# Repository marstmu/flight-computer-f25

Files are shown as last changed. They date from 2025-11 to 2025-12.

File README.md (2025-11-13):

# MARS Flight Computer F25

Use Export KiCad Images Workflow

---

<div align="center">
  <div>
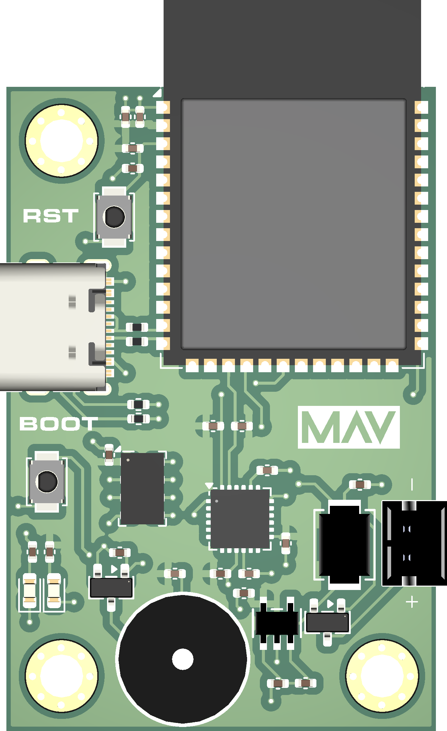
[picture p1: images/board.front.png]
    
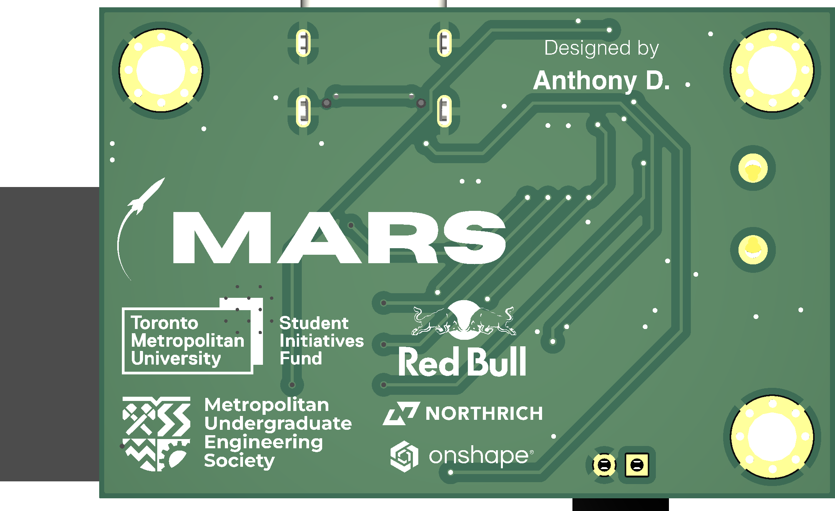
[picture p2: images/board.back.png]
    
    <p><em>3D Render</em></p>
  </div>
  <br>

  <div>
    Schematic<br>
    <p><em>Schematic</em></p>
  </div>
  <br>
  
  <div>
    Front
    Back<br>
    <em>Footprint</em>
  </div>
</div>

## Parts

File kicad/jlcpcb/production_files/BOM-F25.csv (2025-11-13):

Comment | Designator | Footprint | LCSC | Quantity
0.1uF | C2,C5,C7,C9 | C_0402_1005Metric | C1525 | 4
100k | R5,R8,R9 | C_0402_1005Metric | C25741 | 3
10k | R11 | C_0402_1005Metric | C25744 | 1
10nF | C4 | C_0402_1005Metric | C15195 | 1
10uF | C1,C10,C8 | C_0402_1005Metric | C15525 | 3
1k | R1,R4 | C_0402_1005Metric | C11702 | 2
1uF | C3 | C_0402_1005Metric | C52923 | 1
2.2nF | C6 | C_0402_1005Metric | C84703 | 1
27 | R16,R17 | R_0402_1005Metric | C25100 | 2
2k | R7 | C_0402_1005Metric | C4109 | 1
4.7k | R2,R3 | C_0402_1005Metric | C25900 | 2
5.1k | R12,R6 | R_0402_1005Metric | C25905 | 2
AP2112K-3.3 | U5 | SOT_RG1_DIO | C3021085 | 1
B2B-PH-K-S | J3 | JST_B2B-PH-K-S | C131337 | 1
BOOT | SW2 | SW_SPST_B3U-1000P | C231329 | 1
DMG3415U | Q2 | SOT-23 | C7202986 | 1
ESP32-S3-WROOM-1-N8 | U4 | ESP32-S3-WROOM-1 | C2913198 | 1
HNB09A03 | LS1 | HNB09A03 | C96102 | 1
IRLML6244 | Q1 | SOT-23 | C5123965 | 1
LED | D1 | LED_0603_1608Metric | C2288 | 1
LED | D2 | LED_0603_1608Metric | C2290 | 1
MBRS130LT3G | CR1 | DIODE_SMB_2L_ONS | C51771 | 1
MPU-6050 | U2 | InvenSense_QFN-24_4x4mm_P0.5mm | C24112 | 1
MS5611-01BA | U1 | LGA-8_3x5mm_P1.25mm | C15639 | 1
RESET | SW1 | SW_SPST_B3U-1000P | C231329 | 1
USB_C_Receptacle_USB2.0_16P | J4 | USB_C_Receptacle_Palconn_UTC16-G | C2765186 | 1

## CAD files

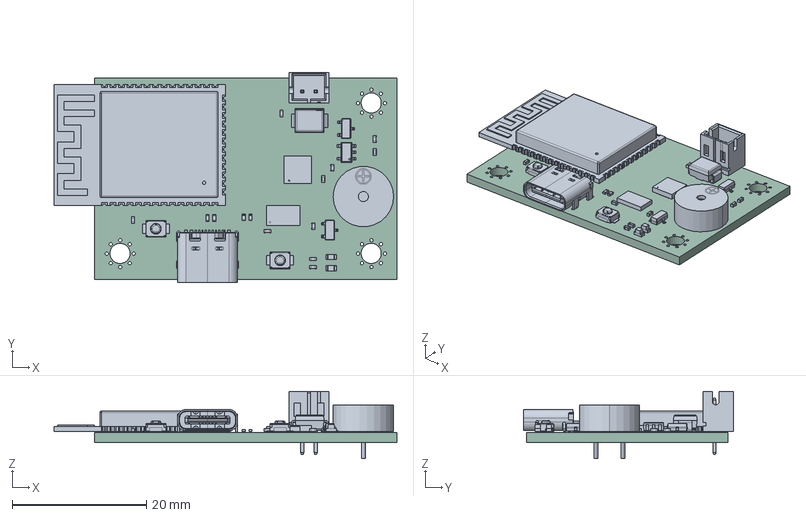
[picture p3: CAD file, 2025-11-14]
images/board.step
51.1 x 31.2 x 10.0 mm
C_0402_1005Metric x 10
SOT-23 x 2
kicad_embedded_C2CC4DB59B260F51541E3CE257640357
ESP32-S3-WROOM-1
board 1.6
R_0402_1005Metric x 4
USB_C_Receptacle_GCT_USB4105-xx-A_16P_TopMnt_Horizontal
LED_0603_1608Metric x 2
MBRS130LT3G
LGA-8_3x5mm_P1.25mm
SW_SPST_B3U-1000P x 2
AP2112K-3.3TRG1--3DModel-STEP-418109
F25_PCB

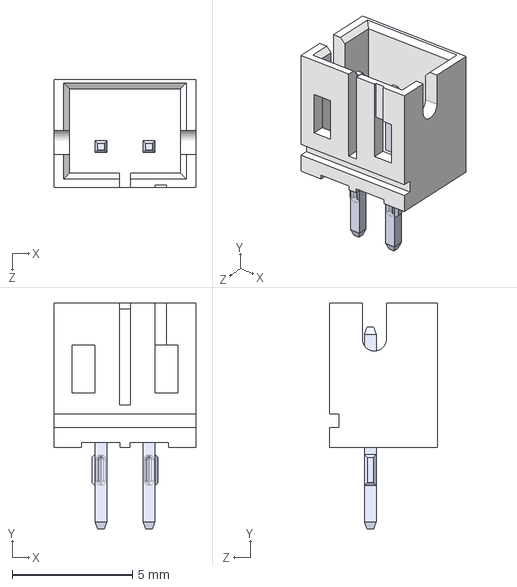
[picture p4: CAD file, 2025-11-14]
kicad/step files/B2B-PH-K-S--3DModel-STEP-56544.STEP
5.90 x 9.40 x 4.50 mm

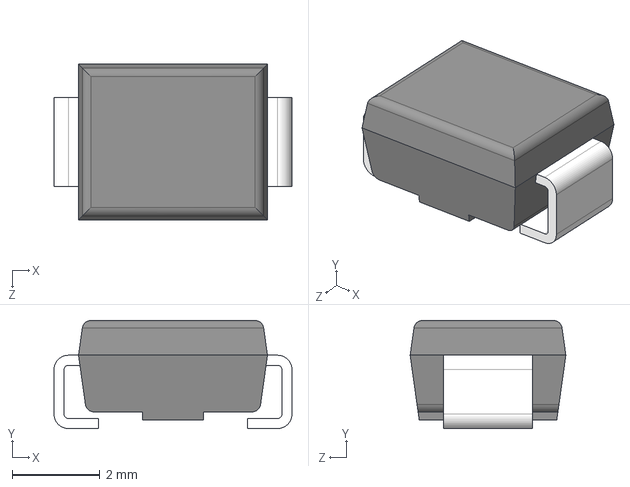
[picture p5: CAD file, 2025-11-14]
kicad/step files/MBRS130LT3G.STEP
5.44 x 2.47 x 3.56 mm

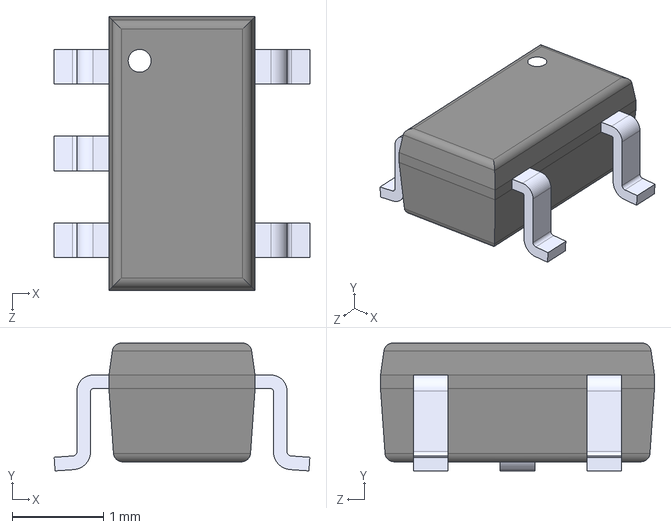
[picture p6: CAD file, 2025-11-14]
kicad/step files/AP2112K-3.3TRG1--3DModel-STEP-418109.STEP
2.80 x 1.40 x 3.00 mm

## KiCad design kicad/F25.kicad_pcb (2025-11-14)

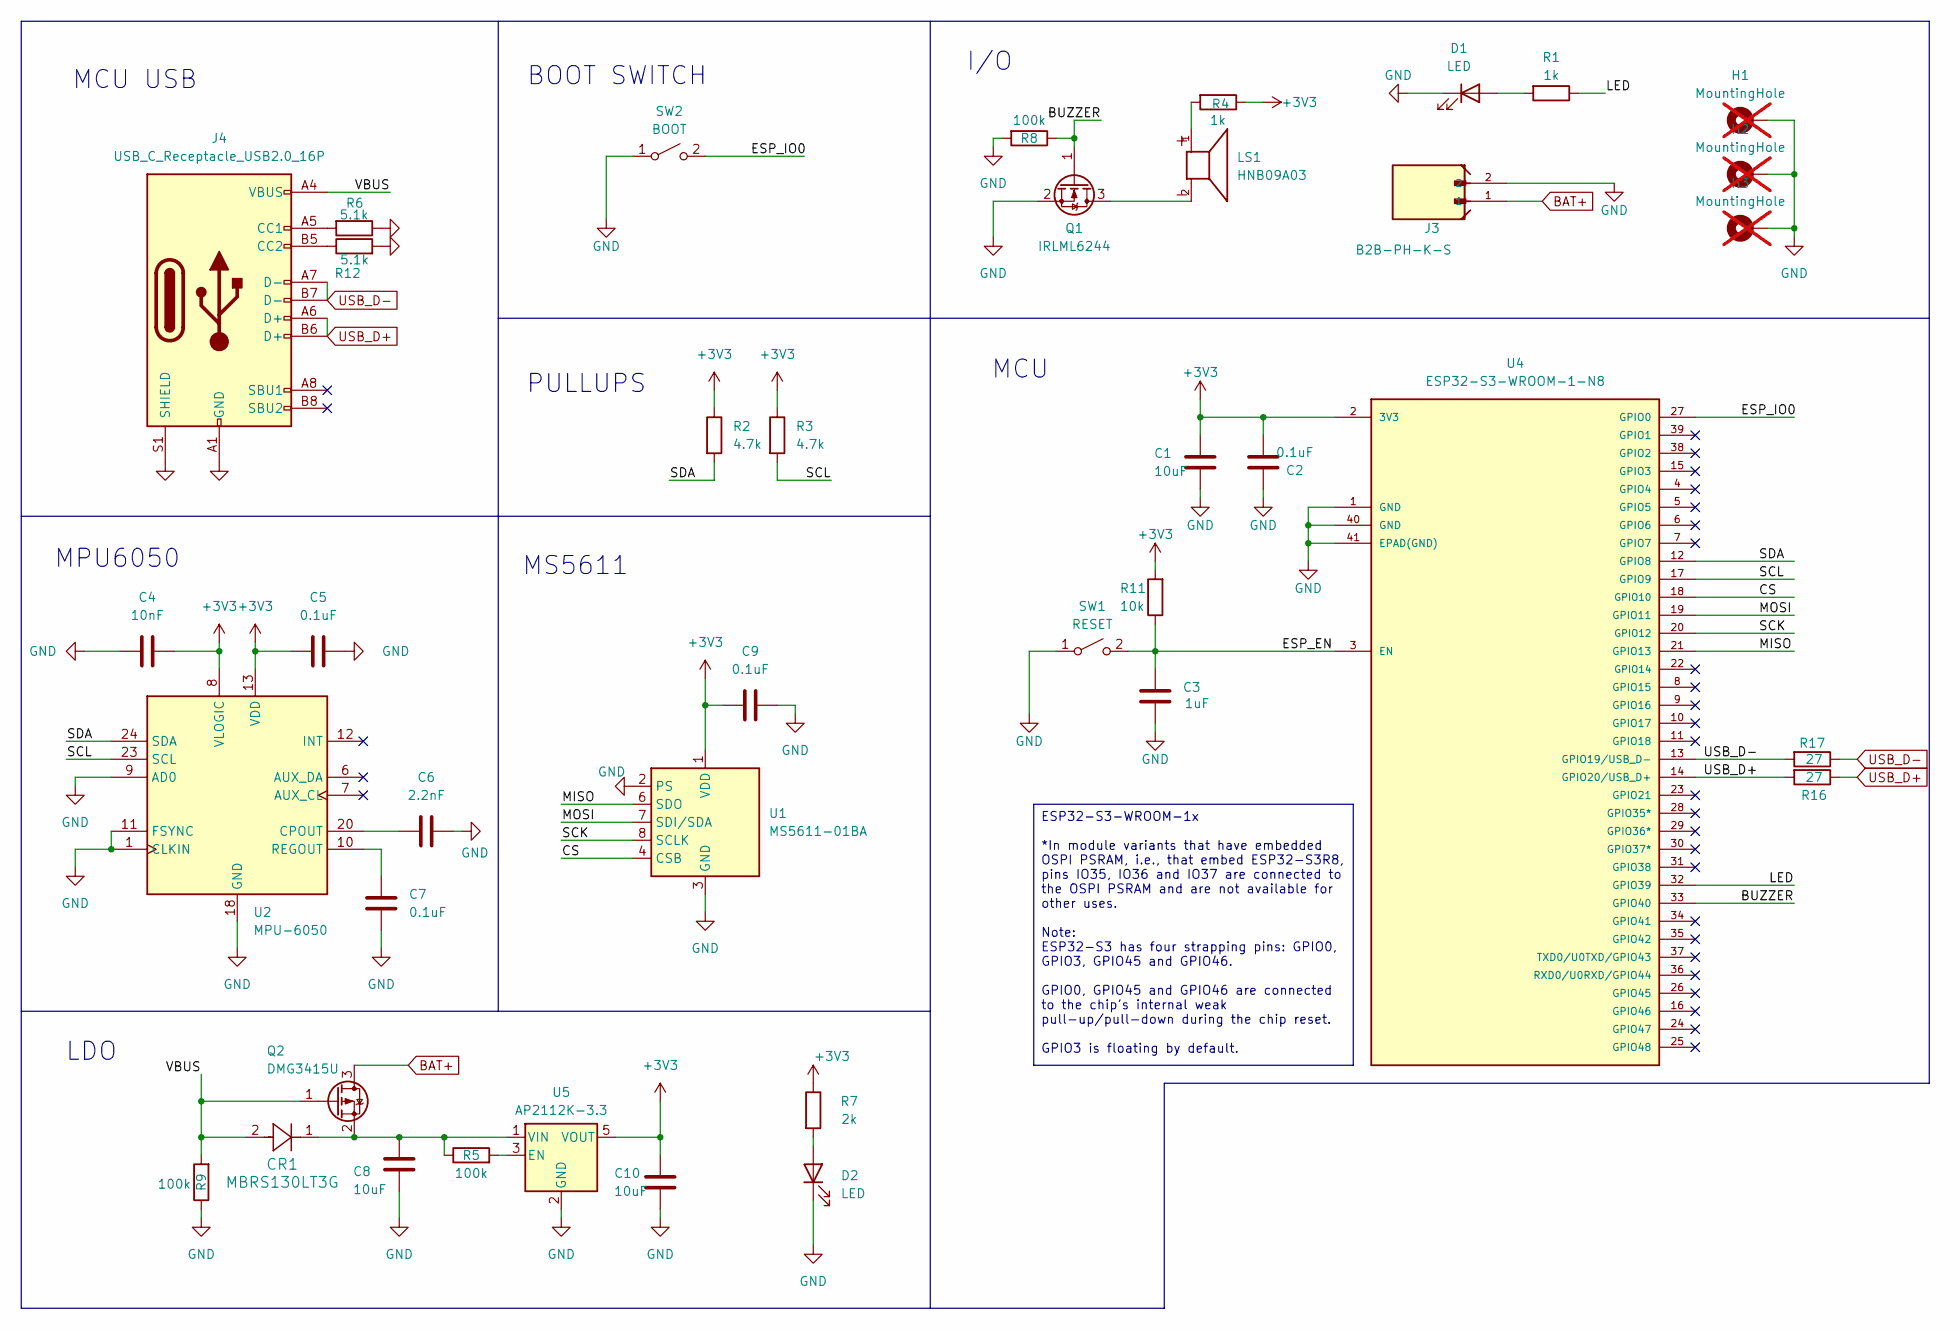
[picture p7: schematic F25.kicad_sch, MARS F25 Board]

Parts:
C1, C8, C10: 10uF; C_0402_1005Metric; LCSC C15525
C2, C5, C7, C9: 0.1uF; C_0402_1005Metric; LCSC C1525
C3: 1uF; C_0402_1005Metric; LCSC C52923
C4: 10nF; C_0402_1005Metric; LCSC C15195
C6: 2.2nF; C_0402_1005Metric; LCSC C84703
CR1: MBRS130LT3G; DIODE_SMB_2L_ONS; LCSC C51771
D1: LED; LED_0603_1608Metric; LCSC C2288
D2: LED; LED_0603_1608Metric; LCSC C2290
H1, H2, H3: MountingHole; hole; not fitted
J3: B2B-PH-K-S; JST_B2B-PH-K-S; LCSC C131337
J4: USB_C_Receptacle_USB2.0_16P; USB_C_Receptacle_Palconn_UTC16-G; LCSC Part # C2765186
LS1: HNB09A03; PARTREV C; LCSC C96102
Q1: IRLML6244; SOT-23; LCSC C5123965
Q2: DMG3415U; SOT-23; LCSC C7202986
R1, R4: 1k; C_0402_1005Metric; LCSC C11702
R2, R3: 4.7k; C_0402_1005Metric; LCSC C25900
R5, R8, R9: 100k; C_0402_1005Metric; LCSC C25741
R6, R12: 5.1k; R_0402_1005Metric; LCSC Part # C25905
R7: 2k; C_0402_1005Metric; LCSC C4109
R11: 10k; C_0402_1005Metric; LCSC C25744
R16, R17: 27; R_0402_1005Metric; LCSC Part # C25100
SW1: RESET; SW_SPST_B3U-1000P; LCSC C231329
SW2: BOOT; SW_SPST_B3U-1000P; LCSC C231329
U1: MS5611-01BA; LGA-8_3x5mm_P1.25mm; LCSC C15639
U2: MPU-6050; InvenSense_QFN-24_4x4mm_P0.5mm; LCSC C24112
U4: ESP32-S3-WROOM-1-N8; ESP32-S3-WROOM-1; LCSC C2913198
U5: AP2112K-3.3; SOT_RG1_DIO; LCSC C3021085

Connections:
+3V3: C1.2, C2.2, C4.2, C5.2, C9.1, C10.2, R2.1, R3.1, R4.1, R7.1, R11.2, U1.1 (VDD), U2.8 (VLOGIC), U2.13 (VDD), U4.2 (3V3), U5.5 (VOUT)
/BUZZER: Q1.1 (G), R8.1, U4.33 (GPIO40)
/CS: U1.4 (CSB), U1.5 (CSB), U4.18 (GPIO10)
/ESP_EN: C3.1, R11.1, SW1.2 (B), U4.3 (EN)
/ESP_IO0: SW2.2 (B), U4.27 (GPIO0)
/LED: R1.1, U4.32 (GPIO39)
/MISO: U1.6 (SDO), U4.21 (GPIO13)
/MOSI: U1.7 (SDI/SDA), U4.19 (GPIO11)
/SCK: U1.8 (SCLK), U4.20 (GPIO12)
/SCL: R3.2, U2.23 (SCL), U4.17 (GPIO9)
/SDA: R2.2, U2.24 (SDA), U4.12 (GPIO8)
/VBUS: CR1.2, J4.A4 (VBUS), J4.A9 (VBUS), J4.B4 (VBUS), J4.B9 (VBUS), Q2.1 (G), R9.2
BAT+: J3.1, Q2.3 (D)
GND: C1.1, C2.1, C3.2, C4.1, C5.1, C6.2, C7.2, C8.1, C9.2, C10.1, D1.1 (K), D2.1 (K), H1.1, H2.1, H3.1, J3.2, J4.A1 (GND), J4.A12 (GND), J4.B1 (GND), J4.B12 (GND), J4.S1 (SHIELD), Q1.2 (S), R6.1, R8.2, R9.1, R12.2, SW1.1 (A), SW2.1 (A), U1.2 (PS), U1.3 (GND), U2.1 (CLKIN), U2.9 (AD0), U2.11 (FSYNC), U2.18 (GND), U4.1 (GND), U4.40 (GND), U4.41 (EPAD(GND)), U5.2 (GND)
unnamed: D1.2 (A), R1.2
unnamed: D2.2 (A), R7.2
unnamed: J4.A5 (CC1), R6.2
unnamed: J4.B5 (CC2), R12.1
unnamed: LS1.1, R4.2
unnamed: LS1.2, Q1.3 (D)
unnamed: C8.2, CR1.1, Q2.2 (S), R5.1, U5.1 (VIN)
unnamed: C6.1, U2.20 (CPOUT)
unnamed: C7.1, U2.10 (REGOUT)
unnamed: R5.2, U5.3 (EN)
USB_D+: J4.A6 (D+), J4.B6 (D+), R16.1, R16.2, U4.14 (GPIO20/USB_D+)
USB_D-: J4.A7 (D-), J4.B7 (D-), R17.1, R17.2, U4.13 (GPIO19/USB_D-)

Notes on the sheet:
I/O
MCU
PULLUPS
MPU6050
BOOT SWITCH
MS5611
LDO
MCU USB
ESP32-S3-WROOM-1x *In module variants that have embedded OSPI PSRAM, i.e., that embed ESP32-S3R8, pins IO35, IO36 and IO37 are connected to the OSPI PSRAM and are not available for other uses. Note: ESP32-S3 has four strapping pins: GPIO0, GPIO3, GPIO45 and GPIO46. GPIO0, GPIO45 and GPIO46 are conn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

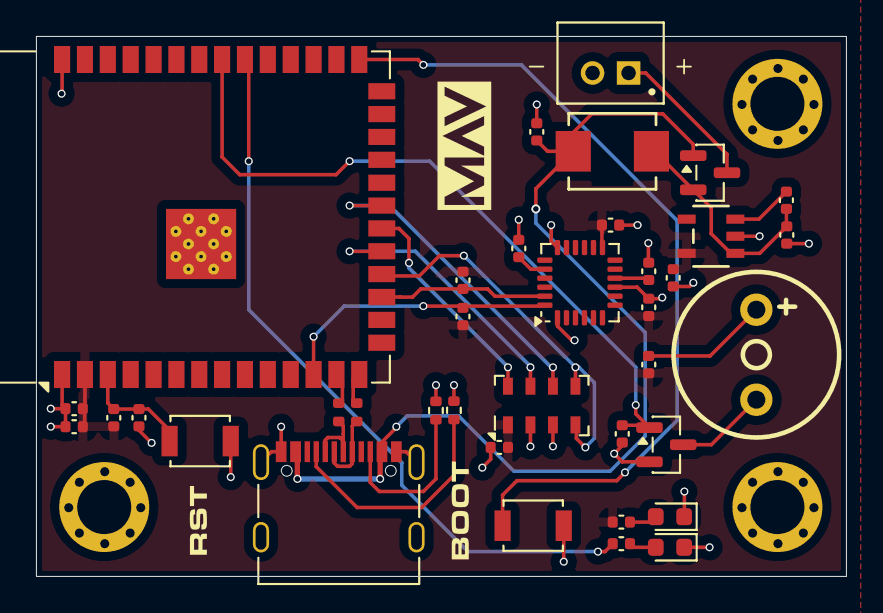
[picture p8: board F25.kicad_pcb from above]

Board: 2 copper layers, 45.0 x 30.0 mm, 40 parts (0 on the bottom side), 26 nets.

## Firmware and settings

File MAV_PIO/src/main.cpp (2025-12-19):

/*
   MARS BOARD MAV - ESP32-S3 Flight Computer (PlatformIO)

   SAFE MODE (No USB MSC):
   - Pre-launch RAM cache (ring buffer) so you get data before launch
   - Launch detection -> open a new CSV and dump cache
   - Apogee detection -> mark event in CSV
   - Landing detection -> log a bit more -> close file
   - After file is closed -> start WiFi AP + Web dashboard + download endpoints

   MS5611:
   - Non-blocking sampling state machine (no delays in handlers)
   - Second-order temperature compensation
   - ASL altitude: altitude_asl = ref_alt_asl + delta_h
*/

#include <Arduino.h>
#include <Wire.h>
#include <ms5611.h>
#include <WiFi.h>
#include <WebServer.h>
#include <FFat.h>
#include <esp_system.h> // esp_random()

#include <I2Cdev.h>
#include <MPU6050_6Axis_MotionApps20.h>
#include <helper_3dmath.h>

// -------------------- PIN CONFIG --------------------
const int SDA_PIN = 8;
const int SCL_PIN = 9;



const int LED_PIN = 39;

// -------------------- ACCESS POINT --------------------
const char* ap_ssid = "MAV_TELEM";
const char* ap_pass = "RocketGroup1!"; // must be >=8 chars
WebServer server(80);
bool apMode = false;

// If true: AP runs pre-launch for setup; turns off during flight; turns back on after landing.
static constexpr bool WIFI_ON_GROUND = true;
static constexpr bool WIFI_OFF_DURING_FLIGHT = false;

// -------------------- MPU6050 DMP --------------------
MPU6050 mpu;
bool dmpReady = false;
uint8_t fifoBuffer[64];
uint16_t packetSize = 0;

Quaternion q;
VectorFloat gravity;
float ypr[3];   // yaw, pitch, roll (rad)
float ypr_offset[3] = {0, 0, 0};

int16_t ax_raw, ay_raw, az_raw;
int16_t gx_raw, gy_raw, gz_raw;
int16_t temp_raw;
float temp_mpu;

// MPU6050 scaling
const float ACCEL_SCALE = 2048.0f; // ±16g
const float GYRO_SCALE  = 16.4f;   // ±2000deg/s

// Device offsets
const int16_t DEV_ACCEL_X_OFFSET = 844;
const int16_t DEV_ACCEL_Y_OFFSET = 1341;
const int16_t DEV_ACCEL_Z_OFFSET = 743;
const int16_t DEV_GYRO_X_OFFSET  = 30;
const int16_t DEV_GYRO_Y_OFFSET  = 67;
const int16_t DEV_GYRO_Z_OFFSET  = -3;

// -------------------- LED CONTROL --------------------
unsigned long lastBlinkTime = 0;
const unsigned long BLINK_FAST = 150;
const unsigned long BLINK_SLOW = 1000;

// -------------------- FLIGHT STATE / LOGGING --------------------
enum FlightState : uint8_t {
  ST_GROUND = 0,  // cache; (optional) AP on for setup
  ST_FLIGHT = 1,  // logging; AP off
  ST_LANDED = 2,  // post-land logging window
  ST_DONE   = 3   // file closed; AP on for download
};

FlightState flightState = ST_GROUND;

// Logging cadence
static constexpr uint32_t LOG_HZ = 50;
static constexpr uint32_t LOG_INTERVAL_MS = 1000 / LOG_HZ;

// Pre-launch cache
static constexpr uint32_t CACHE_SECONDS = 4;
static constexpr uint16_t CACHE_SAMPLES = LOG_HZ * CACHE_SECONDS;

// Detection tuning (adjust after ground tests)
static constexpr float LAUNCH_ALT_THRESH_M = 8.0f;
static constexpr float LAUNCH_VEL_THRESH_MPS = 8.0f;
static constexpr uint16_t LAUNCH_CONFIRM_SAMPLES = 5;

static constexpr float APOGEE_VEL_NEG_THRESH_MPS = -1.5f;
static constexpr float APOGEE_DROP_THRESH_M = 1.5f;
static constexpr uint16_t APOGEE_CONFIRM_SAMPLES = 8;

static constexpr float LAND_VEL_ABS_THRESH_MPS = 2.0f;
static constexpr float LAND_ALT_RANGE_M = 2.0f;
static constexpr uint32_t LAND_STABLE_MS = 2500;
static constexpr uint32_t LAND_AFTER_APOGEE_DELAY_MS = 8000; // 5–10s (pick 5000..10000)

static constexpr uint32_t POST_LAND_LOG_MS = 3000;

struct Sample {
  uint32_t t_ms;
  float h_m;        // height (relative to start), m
  float alt_asl_m;  // ASL altitude, m
  float vel_mps;    // filtered vertical speed, m/s
  float p_mbar;
  float t_ms5611_c;
  float t_mpu_c;
  float ax_g, ay_g, az_g;
  float pitch_deg, roll_deg, yaw_deg;
};

Sample cacheBuf[CACHE_SAMPLES];
uint16_t cacheHead = 0;
bool cacheFilled = false;

File logFile;
bool logOpen = false;
char currentLogPath[40] = {0};

uint32_t nextLogMs = 0;

// Detection internals
bool launchDetected = false;
bool apogeeDetected = false;
bool landingDetected = false;

float maxHeight_m = -1e9f;
uint16_t launchConfirm = 0;
uint16_t apogeeConfirm = 0;
uint32_t apogeeAtMs = 0;

uint32_t landStableStartMs = 0;
float landAltRef = 0.0f;
uint32_t landedAtMs = 0;

// Velocity estimation (windowed average altitude -> velocity)
// Computes v = (avg(h) - avg(prev h)) / dt across a window to suppress baro noise.
static constexpr uint8_t VELWIN = 50;   // window length in samples (LOG_HZ=50 => 25 samples = 0.50 s)

float hWin[VELWIN] = {0};
uint32_t tWin[VELWIN] = {0};
uint8_t velIdx = 0;
uint8_t velCount = 0;

float lastAvgH = 0.0f;
uint32_t lastAvgT = 0;
float velfilt = 0.0f; // optional extra low-pass after windowing
// Latest computed vertical speed for dashboard (updated in loop logging cadence)
volatile float latest_vel_mps = 0.0f;

// -------------------- FORWARD DECLARATIONS --------------------


void read_mpu_raw();
void convert_accel_to_g(float &ax_g, float &ay_g, float &az_g);
void convert_gyro_to_degs(float &gx_degs, float &gy_degs, float &gz_degs);
void read_dmp();
void zeroYPR();
void get_adjusted_ypr(float &yaw_adj, float &pitch_adj, float &roll_adj);

void updateLED();
String htmlPage();
void handleRoot();
void handleSetAltitude();
void handleZeroYPR();
void handleData();
void handleDeleteLogs();

void startAPAndServer();
void handleReset();
void stopAPAndServer();

void cachePush(const Sample &s);
void dumpCacheToFile();
bool openNewLogFile();
void closeLogFileSafe();
void writeCsvHeader();
void writeCsvRow(const Sample &s, const char* eventTag);

float computeVerticalSpeed(float h_now, uint32_t now_ms);
Sample makeSample(float vel_mps_now);
const char* flightStateName(FlightState st);

void updateFlightStateAndLogging(const Sample &s);

// -------------------- MS5611 low-level --------------------


// -------------------- MPU Raw + DMP --------------------
void read_mpu_raw() {
  mpu.getMotion6(&ax_raw, &ay_raw, &az_raw, &gx_raw, &gy_raw, &gz_raw);
  temp_raw = mpu.getTemperature();
  temp_mpu = temp_raw / 340.0f + 36.53f;
}

void convert_accel_to_g(float &ax_g, float &ay_g, float &az_g) {
  ax_g = (float)ax_raw / ACCEL_SCALE;
  ay_g = (float)ay_raw / ACCEL_SCALE;
  az_g = (float)az_raw / ACCEL_SCALE;
}

void convert_gyro_to_degs(float &gx_degs, float &gy_degs, float &gz_degs) {
  gx_degs = (float)gx_raw / GYRO_SCALE;
  gy_degs = (float)gy_raw / GYRO_SCALE;
  gz_degs = (float)gz_raw / GYRO_SCALE;
}

void read_dmp() {
  if (!dmpReady) return;

  uint8_t intStatus = mpu.getIntStatus();
  uint16_t fifoCount = mpu.getFIFOCount();

  if (intStatus & 0x10) {
    mpu.resetFIFO();
    delay(10);
    return;
  }

  while (fifoCount >= packetSize) {
    mpu.getFIFOBytes(fifoBuffer, packetSize);
    mpu.dmpGetQuaternion(&q, fifoBuffer);
    mpu.dmpGetGravity(&gravity, &q);
    mpu.dmpGetYawPitchRoll(ypr, &q, &gravity);

    read_mpu_raw();
    fifoCount = mpu.getFIFOCount();
  }
}

void zeroYPR() {
  ypr_offset[0] = ypr[0] * 180.0f / M_PI;
  ypr_offset[1] = ypr[1] * 180.0f / M_PI;
  ypr_offset[2] = ypr[2] * 180.0f / M_PI;
}

void get_adjusted_ypr(float &yaw_adj, float &pitch_adj, float &roll_adj) {
  yaw_adj   = (ypr[0] * 180.0f / M_PI) - ypr_offset[0];
  pitch_adj = (ypr[1] * 180.0f / M_PI) - ypr_offset[1];
  roll_adj  = (ypr[2] * 180.0f / M_PI) - ypr_offset[2];
}

// -------------------- Logging / state --------------------
const char* flightStateName(FlightState st) {
  switch (st) {
    case ST_GROUND: return "GROUND";
    case ST_FLIGHT: return "FLIGHT";
    case ST_LANDED: return "LANDED";
    case ST_DONE:   return "DONE";
    default:        return "UNKNOWN";
  }
}

void cachePush(const Sample &s) {
  cacheBuf[cacheHead] = s;
  cacheHead = (cacheHead + 1) % CACHE_SAMPLES;
  if (cacheHead == 0) cacheFilled = true;
}

void writeCsvHeader() {
  if (!logFile) return;
  logFile.println("t_ms,h_m,alt_asl_m,vel_mps,p_mbar,t_ms5611_c,t_mpu_c,ax_g,ay_g,az_g,pitch_deg,roll_deg,yaw_deg,event");
}

void writeCsvRow(const Sample &s, const char* eventTag) {
  if (!logFile) return;

  char line[240];
  int n = snprintf(line, sizeof(line),
    "%lu,%.3f,%.3f,%.3f,%.2f,%.2f,%.2f,%.3f,%.3f,%.3f,%.2f,%.2f,%.2f,%s",
    (unsigned long)s.t_ms,
    s.h_m, s.alt_asl_m, s.vel_mps,
    s.p_mbar,
    s.t_ms5611_c, s.t_mpu_c,
    s.ax_g, s.ay_g, s.az_g,
    s.pitch_deg, s.roll_deg, s.yaw_deg,
    (eventTag ? eventTag : "")
  );
  if (n > 0) logFile.println(line);
}

void dumpCacheToFile() {
  if (!logFile) return;

  uint16_t count = cacheFilled ? CACHE_SAMPLES : cacheHead;
  uint16_t start = cacheFilled ? cacheHead : 0;

  for (uint16_t i = 0; i < count; i++) {
    uint16_t idx = (start + i) % CACHE_SAMPLES;
    writeCsvRow(cacheBuf[idx], "CACHE");
  }
}

bool openNewLogFile() {
  if (logOpen) return true;

  currentLogPath[0] = 0;

  uint32_t r = esp_random();
  uint32_t m = millis();
  snprintf(currentLogPath, sizeof(currentLogPath), "/flight_%08lX_%08lX.csv",
           (unsigned long)r, (unsigned long)m);

  logFile = FFat.open(currentLogPath, FILE_WRITE);
  if (!logFile) {
    currentLogPath[0] = 0;
    logOpen = false;
    return false;
  }

  logOpen = true;
  writeCsvHeader();
  dumpCacheToFile();
  logFile.flush();
  return true;
}

void closeLogFileSafe() {
  if (!logOpen) return;
  logFile.flush();
  logFile.close();
  logOpen = false;
}

float computeVerticalSpeed(float hnow, uint32_t nowms) {
  // Push into ring buffer
  hWin[velIdx] = hnow;
  tWin[velIdx] = nowms;
  velIdx = (uint8_t)((velIdx + 1) % VELWIN);
  if (velCount < VELWIN) velCount++;

  // Until window is full, don't output noisy velocity
  if (velCount < VELWIN) {
    lastAvgH = hnow;
    lastAvgT = nowms;
    velfilt = 0.0f;
    return 0.0f;
  }

  // Compute average altitude and average time over the window
  float sumH = 0.0f;
  uint32_t sumT = 0;
  for (uint8_t i = 0; i < VELWIN; i++) {
    sumH += hWin[i];
    sumT += tWin[i];
  }
  const float avgH = sumH / (float)VELWIN;
  const uint32_t avgT = sumT / (uint32_t)VELWIN;

  // Differentiate the averaged signal
  if (lastAvgT == 0) {
    lastAvgT = avgT;
    lastAvgH = avgH;
    return 0.0f;
  }

  uint32_t dtms = avgT - lastAvgT;
  if (dtms < 5) return velfilt; // avoid divide by tiny dt / repeated timestamps

  const float dt = dtms / 1000.0f;
  const float v = (avgH - lastAvgH) / dt;

  // Optional extra smoothing on top of the window (can set VELALPHA=1.0f to disable)
  const float VELALPHA = 0.35f;
  velfilt = VELALPHA * v + (1.0f - VELALPHA) * velfilt;

  lastAvgT = avgT;
  lastAvgH = avgH;
  return velfilt;
}

Sample makeSample(float vel_mps_now) {
  Sample s{};
  s.t_ms = millis();

  s.h_m = isfinite(height_agl_m) ? (float)height_agl_m : 0.0f;
  s.alt_asl_m = isfinite(altitude_asl_m) ? (float)altitude_asl_m : 0.0f;
  s.vel_mps = vel_mps_now;

  s.p_mbar = isfinite(ms5611_pressure_mbar) ? (float)ms5611_pressure_mbar : 0.0f;
  s.t_ms5611_c = isfinite(ms5611_temp_c) ? (float)ms5611_temp_c : 0.0f;
  s.t_mpu_c = (float)temp_mpu;

  float ax_g, ay_g, az_g;
  convert_accel_to_g(ax_g, ay_g, az_g);
  s.ax_g = ax_g; s.ay_g = ay_g; s.az_g = az_g;

  s.pitch_deg = ypr[1] * 180.0f / M_PI;
  s.roll_deg  = ypr[2] * 180.0f / M_PI;
  s.yaw_deg = ypr[0] * 180.0f / M_PI;

  return s;
}

void updateFlightStateAndLogging(const Sample &s) {
  // Always keep a cache until launch
  if (!launchDetected) cachePush(s);

  // Track max height
  if (s.h_m > maxHeight_m) maxHeight_m = s.h_m;

  // ---------------- LAUNCH DETECT ----------------
  if (!launchDetected) {
    bool cond = (s.h_m > LAUNCH_ALT_THRESH_M) && (s.vel_mps > LAUNCH_VEL_THRESH_MPS);
    if (cond) launchConfirm++;
    else if (launchConfirm > 0) launchConfirm--;

    if (launchConfirm >= LAUNCH_CONFIRM_SAMPLES) {
      launchDetected = true;
      flightState = ST_FLIGHT;

      if (openNewLogFile()) {
        writeCsvRow(s, "EVENT_LAUNCH");
        logFile.flush();
      }

      if (WIFI_OFF_DURING_FLIGHT && apMode) {
        stopAPAndServer();
      }
    }
  }

  // ---------------- FLIGHT LOGGING ----------------
  if (flightState == ST_FLIGHT && logOpen) {
    const char* tag = "";

    // APOGEE DETECT (requires descent + drop from max)
    if (!apogeeDetected) {
      bool apCond = (s.vel_mps < APOGEE_VEL_NEG_THRESH_MPS) && ((maxHeight_m - s.h_m) > APOGEE_DROP_THRESH_M);
      if (apCond) apogeeConfirm++;
      else if (apogeeConfirm > 0) apogeeConfirm--;

      if (apogeeConfirm >= APOGEE_CONFIRM_SAMPLES) {
        apogeeDetected = true;
        apogeeAtMs = millis();
        tag = "EVENT_APOGEE";
      }
    }

    writeCsvRow(s, tag);

    // Periodic flush (limits loss, avoids flush every line)
    static uint32_t lastFlushMs = 0;
    uint32_t now = millis();
    if (now - lastFlushMs >= 1000) {
      lastFlushMs = now;
      logFile.flush();
    }
  }

  // ---------------- LANDING DETECT ----------------
  if (flightState == ST_FLIGHT && apogeeDetected && !landingDetected &&
    (millis() - apogeeAtMs) >= LAND_AFTER_APOGEE_DELAY_MS) {
    bool velOk = fabsf(s.vel_mps) < LAND_VEL_ABS_THRESH_MPS;

    if (velOk) {
      if (landStableStartMs == 0) {
        landStableStartMs = s.t_ms;
        landAltRef = s.h_m;
      } else {
        bool altOk = fabsf(s.h_m - landAltRef) < LAND_ALT_RANGE_M;
        if (!altOk) {
          landStableStartMs = s.t_ms;
          landAltRef = s.h_m;
        } else if ((s.t_ms - landStableStartMs) >= LAND_STABLE_MS) {
          landingDetected = true;
          flightState = ST_LANDED;
          landedAtMs = millis();

          if (logOpen) {
            writeCsvRow(s, "EVENT_LAND");
            logFile.flush();
          }
        }
      }
    } else {
      landStableStartMs = 0;
    }
  }

  // ---------------- POST-LANDING WINDOW ----------------
  if (flightState == ST_LANDED) {
    if (logOpen) {
      writeCsvRow(s, "POST_LAND");
    }

    if (millis() - landedAtMs >= POST_LAND_LOG_MS) {
      if (logOpen) {
        writeCsvRow(s, "EVENT_CLOSE");
        closeLogFileSafe();
      }
      flightState = ST_DONE;

      // AP on for recovery/download
      if (!apMode) {
        startAPAndServer();
      }
    }
  }
}

// -------------------- WiFi / Server --------------------

// Optional: fixed AP IP (nice for phones). Comment out if you prefer default 192.168.4.1.
static const IPAddress AP_IP(192, 168, 4, 1);
static const IPAddress AP_GW(192, 168, 4, 1);
static const IPAddress AP_SUBNET(255, 255, 255, 0);

// Helper: start SoftAP with some explicit params (channel/max conn from Arduino-ESP32 WiFi API) [web:160]
static bool startSoftAP() {
  WiFi.mode(WIFI_AP);
  delay(50);

  // Optional static IP
  WiFi.softAPConfig(AP_IP, AP_GW, AP_SUBNET); // returns bool; ignore if it fails

  const int channel = 1;
  const int hidden = 0;
  const int maxConn = 4;

  bool ok;
  if (ap_pass == nullptr || strlen(ap_pass) == 0) {
    ok = WiFi.softAP(ap_ssid, nullptr, channel, hidden, maxConn);
  } else {
    ok = WiFi.softAP(ap_ssid, ap_pass, channel, hidden, maxConn);
  }
  return ok;
}

void stopAPAndServer() {
  // Stop HTTP server first
  server.stop();

  // Explicitly stop SoftAP, optionally powering off WiFi radio afterward [web:160]
  WiFi.softAPdisconnect(true); // true => turn WiFi off too
  delay(50);

  WiFi.mode(WIFI_OFF);
  delay(50);

  apMode = false;
}

void startAPAndServer() {
  // (Re)start AP
  apMode = startSoftAP();

  // If AP start failed, don't start routes/server
  if (!apMode) {
    return;
  }

  // ---- Core routes ----
  server.on("/", handleRoot);
  server.on("/data", handleData);
  server.on("/setAltitude", HTTP_POST, handleSetAltitude);
  server.on("/zeroYPR", HTTP_POST, handleZeroYPR);
  server.on("/reset", HTTP_POST, handleReset);

  // ---- Delete all CSV logs ----
  server.on("/deleteLogs", HTTP_POST, handleDeleteLogs);

  // ---- Minimal status endpoint ----
  server.on("/status", HTTP_GET, []() {
    String json = "{";
    json += "\"state\":\"" + String(flightStateName(flightState)) + "\",";
    json += "\"launch\":" + String(launchDetected ? "true" : "false") + ",";
    json += "\"apogee\":" + String(apogeeDetected ? "true" : "false") + ",";
    json += "\"landed\":" + String(landingDetected ? "true" : "false") + ",";
    json += "\"log_open\":" + String(logOpen ? "true" : "false") + ",";
    json += "\"log_file\":\"" + String(currentLogPath) + "\"";
    json += "}";
    server.send(200, "application/json", json);
  });

  // ---- List logs (simple HTML) ----
  server.on("/logs", HTTP_GET, []() {
    String out;
    out.reserve(3500);
    out += "<html><head><meta name='viewport' content='width=device-width, initial-scale=1'></head><body>";
    out += "<h3>Logs</h3>";
    out += "<p><a href='/latest'>Download latest</a></p>";
    out += "<form method='POST' action='/deleteLogs' onsubmit='return confirm(\"Delete ALL CSV logs?\")'>"
           "<button type='submit' style='background:#e74c3c;color:white;border:none;padding:10px;border-radius:6px;'>Delete all CSV logs</button>"
           "</form>";
    out += "<ul>";

    File root = FFat.open("/");
    if (!root || !root.isDirectory()) {
      out += "<li>FFat open root failed</li>";
    } else {
      File f = root.openNextFile();
      while (f) {
        String name = String(f.name());
        size_t sz = f.size();
        out += "<li><a href='/download?file=" + name + "'>" + name + "</a> (" + String((unsigned long)sz) + " bytes)</li>";
        f.close();                 // IMPORTANT
        f = root.openNextFile();
      }
      root.close();                // IMPORTANT
    }

    out += "</ul></body></html>";
    server.send(200, "text/html", out);
  });

  // ---- Download: /download?file=/flight_xxx.csv ----
  server.on("/download", HTTP_GET, []() {
    if (!server.hasArg("file")) {
      server.send(400, "text/plain", "Missing file parameter");
      return;
    }
    String path = server.arg("file");
    if (!path.startsWith("/")) path = "/" + path;

    File f = FFat.open(path, "r");
    if (!f) {
      server.send(404, "text/plain", "File not found");
      return;
    }

    String fname = String(f.name());
    if (fname.startsWith("/")) fname = fname.substring(1);

    server.sendHeader("Content-Disposition", "attachment; filename=\"" + fname + "\"");
    server.streamFile(f, "text/csv");
    f.close();
  });

  // ---- Best-effort: download latest finished log ----
  server.on("/latest", HTTP_GET, []() {
    // Prefer currentLogPath if it exists and is closed
    if (currentLogPath[0] != 0 && !logOpen) {
      File f = FFat.open(currentLogPath, "r");
      if (f) {
        String fname = String(f.name());
        if (fname.startsWith("/")) fname = fname.substring(1);
        server.sendHeader("Content-Disposition", "attachment; filename=\"" + fname + "\"");
        server.streamFile(f, "text/csv");
        f.close();
        return;
      }
    }

    // Otherwise pick largest /flight_*.csv
    String bestName;
    size_t bestSize = 0;

    File root = FFat.open("/");
    if (root) {
      File f = root.openNextFile();
      while (f) {
        String name = String(f.name());
        size_t sz = f.size();
        if (name.startsWith("/flight_") && name.endsWith(".csv") && sz > bestSize) {
          bestSize = sz;
          bestName = name;
        }
        f.close();
        f = root.openNextFile();
      }

      root.close();
    }

    if (bestName.length() == 0) {
      server.send(404, "text/plain", "No flight logs found");
      return;
    }

    File f = FFat.open(bestName, "r");
    if (!f) {
      server.send(404, "text/plain", "File not found");
      return;
    }

    String fname = bestName;
    if (fname.startsWith("/")) fname = fname.substring(1);
    server.sendHeader("Content-Disposition", "attachment; filename=\"" + fname + "\"");
    server.streamFile(f, "text/csv");
    f.close();
  });

  server.setContentLength(CONTENT_LENGTH_UNKNOWN);
  server.begin();
}

// -------------------- LED --------------------
void updateLED() {
  unsigned long now = millis();

  if (flightState == ST_FLIGHT) {
    digitalWrite(LED_PIN, HIGH); // solid ON during flight
    return;
  }

  // DONE: slow blink
  if (flightState == ST_DONE) {
    if (now - lastBlinkTime >= BLINK_SLOW) {
      lastBlinkTime = now;
      digitalWrite(LED_PIN, !digitalRead(LED_PIN));
    }
    return;
  }

  // Ground / landed: blink based on client count (only if AP is on)
  if (!apMode) {
    digitalWrite(LED_PIN, LOW);
    return;
  }

  int clients = WiFi.softAPgetStationNum();
  unsigned long interval = (clients > 0) ? BLINK_SLOW : BLINK_FAST;
  if (now - lastBlinkTime >= interval) {
    lastBlinkTime = now;
    digitalWrite(LED_PIN, !digitalRead(LED_PIN));
  }
}

// -------------------- HTML & Server Handlers --------------------

static const char* ALTITUDE_INPUT_DEFAULT = "95.0";

// New handler forward-declare (add to your forward declarations too)
void handleDeleteLogs();
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
void loop() {
  // Keep MS5611 conversions running
  ms5611_task_update();

  // Update IMU
  read_dmp();
  read_mpu_raw();

  // Logging cadence
  const uint32_t now = millis();
  if ((int32_t)(now - nextLogMs) >= 0) {
    nextLogMs += LOG_INTERVAL_MS;

    float h_now = isfinite(height_agl_m) ? (float)height_agl_m : 0.0f;
    float v_now = computeVerticalSpeed(h_now, now);

    // Publish for dashboard without re-running the estimator in handleData()
    latest_vel_mps = v_now;

    Sample s = makeSample(v_now);
    updateFlightStateAndLogging(s);
  }

  // Web server only when AP is on
  if (apMode) {
    server.handleClient();
  }

  updateLED();
  delay(1);
}

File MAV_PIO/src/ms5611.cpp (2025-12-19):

#include "ms5611.h"
#include <Arduino.h>
#include <SPI.h>

// Outputs updated by baro task
volatile float ms5611_temp_c = NAN;
volatile float ms5611_pressure_mbar = NAN;
volatile float altitude_asl_m = NAN;
volatile float height_agl_m = NAN;

float altitude_filtered = 0.0f;
const float ALT_ALPHA = 0.12f;

uint16_t C[8] = {0};
float ms5611_temp_offset_c = 0.0f;

// Reference for barometric altitude equation
float p0_ref_mbar = 1013.25f;
float t0_ref_k    = 288.15f;
float ref_alt_asl_m = 0.0f;
bool refSet = false;

static constexpr uint8_t CMD_RESET    = 0x1E;
static constexpr uint8_t CMD_PROM_RD  = 0xA0;
static constexpr uint8_t CMD_ADC_READ = 0x00;

// OSR=1024
static constexpr uint8_t CMD_CONV_D1 = 0x44; // pressure
static constexpr uint8_t CMD_CONV_D2 = 0x54; // temperature
static constexpr uint32_t CONV_TIME_MS = 3;

const int CS_PIN  = 10;
const int SCK_PIN = 12;
const int MOSI_PIN = 11;
const int MISO_PIN = 13;

// Baro state machine
uint8_t baro_state_index = 0;       // 0=temp, 1-4=pressure
uint32_t baro_conv_start_ms = 0;
bool baro_waiting = false;
uint32_t last_D1 = 0;
uint32_t last_D2 = 0;
bool have_D2 = false;

void ms5611_reset() {
  digitalWrite(CS_PIN, LOW);
  SPI.transfer(CMD_RESET);
  digitalWrite(CS_PIN, HIGH);
  delay(4);
}

void ms5611_read_prom() {
  for (int i = 0; i < 8; i++) {
    uint8_t addr = CMD_PROM_RD + (i * 2);
    digitalWrite(CS_PIN, LOW);
    SPI.transfer(addr);
    uint8_t msb = SPI.transfer(0x00);
    uint8_t lsb = SPI.transfer(0x00);
    digitalWrite(CS_PIN, HIGH);
    C[i] = (uint16_t(msb) << 8) | lsb;
    delay(2);
  }
}

void ms5611_start_conversion(uint8_t cmd) {
  digitalWrite(CS_PIN, LOW);
  SPI.transfer(cmd);
  digitalWrite(CS_PIN, HIGH);
  baro_conv_start_ms = millis();
  baro_waiting = true;
}

uint32_t ms5611_read_adc() {
  digitalWrite(CS_PIN, LOW);
  SPI.transfer(CMD_ADC_READ);
  uint8_t b1 = SPI.transfer(0x00);
  uint8_t b2 = SPI.transfer(0x00);
  uint8_t b3 = SPI.transfer(0x00);
  digitalWrite(CS_PIN, HIGH);
  return (uint32_t(b1) << 16) | (uint32_t(b2) << 8) | b3;
}

// -------------------- MS5611 higher-level --------------------
void ms5611_begin() {
  pinMode(CS_PIN, OUTPUT);
  digitalWrite(CS_PIN, HIGH);

  SPI.begin(SCK_PIN, MISO_PIN, MOSI_PIN, CS_PIN);
  SPI.setDataMode(SPI_MODE0);
  SPI.setFrequency(10000000);

  ms5611_reset();
  ms5611_read_prom();

  baro_state_index = 0;
  have_D2 = false;
  ms5611_start_conversion(CMD_CONV_D2);
}

void ms5611_compute(float &temperature_c, float &pressure_mbar, uint32_t D1, uint32_t D2) {
  const float c1 = float(C[1]);
  const float c2 = float(C[2]);
  const float c3 = float(C[3]);
  const float c4 = float(C[4]);
  const float c5 = float(C[5]);
  const float c6 = float(C[6]);

  float dT = float(int32_t(D2) - int32_t(c5 * 256.0f));
  float TEMP = 2000.0f + (dT * c6) / 8388608.0f;                  // 0.01°C
  float OFF  = c2 * 65536.0f + (c4 * dT) / 128.0f;
  float SENS = c1 * 32768.0f + (c3 * dT) / 256.0f;

  if (TEMP < 2000.0f) {
    float T2 = (dT * dT) / 2147483648.0f;
    float aux = (TEMP - 2000.0f) * (TEMP - 2000.0f);
    float OFF2  = 2.5f * aux;
    float SENS2 = 1.25f * aux;

    if (TEMP < -1500.0f) {
      float aux2 = (TEMP + 1500.0f) * (TEMP + 1500.0f);
      OFF2  += 7.0f  * aux2;
      SENS2 += 5.5f  * aux2;
    }

    TEMP -= T2;
    OFF  -= OFF2;
    SENS -= SENS2;
  }

  float P = (float(D1) * SENS / 2097152.0f - OFF) / 32768.0f;     // 0.01 mbar
  temperature_c = (TEMP * 0.01f) + ms5611_temp_offset_c;
  pressure_mbar = P * 0.01f;
}

void ms5611_task_update() {
  if (!baro_waiting) return;
  if (millis() - baro_conv_start_ms < CONV_TIME_MS) return;

  baro_waiting = false;
  uint32_t adc = ms5611_read_adc();
  if (adc == 0 || adc == 0xFFFFFF) {
    if (baro_state_index == 0) ms5611_start_conversion(CMD_CONV_D2);
    else ms5611_start_conversion(CMD_CONV_D1);
    return;
  }

  if (baro_state_index == 0) {
    last_D2 = adc;
    have_D2 = true;
    baro_state_index = 1;
    ms5611_start_conversion(CMD_CONV_D1);
    return;
  }

  last_D1 = adc;

  if (have_D2) {
    float t_c, p_mbar;
    ms5611_compute(t_c, p_mbar, last_D1, last_D2);

    ms5611_temp_c = t_c;
    ms5611_pressure_mbar = p_mbar;

    if (!refSet && isfinite(p_mbar) && isfinite(t_c)) {
      calibrateAltitudeReference(p_mbar, t_c, 0.0f);
    }

    if (refSet && isfinite(p_mbar)) {
      const float dh = calcDeltaH_m(p_mbar);
      height_agl_m = dh;
      altitude_asl_m = ref_alt_asl_m + dh;
      altitude_asl_m = filterAltitude(altitude_asl_m);
    }
  }

  baro_state_index++;
  if (baro_state_index > 4) {
    baro_state_index = 0;
    ms5611_start_conversion(CMD_CONV_D2);
  } else {
    ms5611_start_conversion(CMD_CONV_D1);
  }
}

// -------------------- Altitude math --------------------
void calibrateAltitudeReference(float pressure_mbar, float temp_c, float altitude_asl_m_in) {
  p0_ref_mbar = pressure_mbar;
  t0_ref_k    = temp_c + 273.15f;
  ref_alt_asl_m = altitude_asl_m_in;
  refSet = true;
}

float calcDeltaH_m(float pressure_mbar) {
  if (!refSet || !isfinite(pressure_mbar) || pressure_mbar <= 0) return 0.0f;
  const float EXP = 0.190263f;
  float ratio = p0_ref_mbar / pressure_mbar;
  float dh = (t0_ref_k / 0.0065f) * (powf(ratio, EXP) - 1.0f);
  return dh;
}

float filterAltitude(float a) {
  static bool first = true;
  if (first) { first = false; altitude_filtered = a; }
  altitude_filtered = ALT_ALPHA * a + (1.0f - ALT_ALPHA) * altitude_filtered;
  return altitude_filtered;
}

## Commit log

2025-10-02 First Commit
    Added ESP, MPU6050, MS5611, MBRS130L, EEPROM, and LDO
    [EggtimerIon.kicad_pcb, EggtimerIon.kicad_sch]
2025-10-02 ESP32-WROOM Connections
    Labelled all pins on module
    Added elementary connections and jumpers
    [EggtimerIon.kicad_sch]
2025-10-02 MPU6050 Connections
    Modified IO22 and IO23 on ESP for I2C lines
    Added capacitors and followed general application note for IMU
    [EggtimerIon.kicad_sch]
2025-10-02 MS6511 Connections
    Added capacitors and connected MS5611 to ESP
    [EggtimerIon.kicad_sch]
2025-10-02 CAT24C512 Connections
    Connected EEPROM module to to ESP
    [EggtimerIon.kicad_sch]
2025-10-02 Buzzer, LDO, and JST connected
    Added connections for LDO, JST, and Buzzer (with NFET) to ESP
    [EggtimerIon.kicad_sch]
2025-10-06 Assigned Footprints
    annotated schematic
    assigned footprints
    [EggtimerIon.kicad_sch]
2025-10-06 Initialized footprint
    Assigned some LCSC part numbers
    Need to update ESP32 footprint to THT
    Need to setup 4 layer board settings
    [EggtimerIon.kicad_pcb, EggtimerIon.kicad_sch]
2025-10-06 Lay out almost complete
    aligned parts close to their components
    [EggtimerIon.kicad_pcb]
2025-10-06 Finalized board settings
    added ground planes
    added a few 3d parts
    finalized board settings
    [EggtimerIon.kicad_pcb]
2025-10-12 Added USB C connections
    Added USB C Receptacle
    Added USB to UART bridge
    Added external circuitry for CP2102N module
    [EggtimerIon.kicad_sch]
2025-10-13 Completed first round of layout
    Did a lot of stuff here ok?
    [EggtimerIon.kicad_pcb, EggtimerIon.kicad_sch]
2025-10-14 Updated dates
    Prior to major changes
    [EggtimerIon.kicad_pcb, EggtimerIon.kicad_sch]
2025-10-14 Removed Bridge and Flash
    Deleted USB C Connector
    Deleted EEPROM
    Deleted USB to UART Bridge and external circuitry
    Added mounting holes
    Added changes to layout
    [EggtimerIon.kicad_pcb, EggtimerIon.kicad_sch]
2025-10-14 Refined Layout
    Removed addditional parts
    Shifted MPU6050 to front
    Shifted Transistor and LDO to front
    Added 3D models for MPU6050 and MBRS diode
    [EggtimerIon.kicad_pcb]
2025-10-24 Major Updates
    - Moved all components to front side
    - Added third mounting hole
    - Added most JLC #'s to components
    - Replaced buzzer with one in stock
    - Changed passive components from 1206 to 0402 for assembly
    - Replaced components based on schematic
    - Added zones for power and ground pours
    - Routed tracks and vias
    - Removed designator silk and added labels to jumper pins
    [EggtimerIon.kicad_pcb, EggtimerIon.kicad_sch]
2025-10-26 Refined Schematic
    - determined TBD values
    - connected MS5611 CSB pin to GND
    - added LEDs to GPIO and power
    - added LCSC numbers for new parts
    - assigned footprints for new parts
    [EggtimerIon.kicad_sch]
2025-11-03 Update mounting hole positions
    [EggtimerIon.kicad_pcb]
2025-11-04 Updates
    work towards S3 module
    [EggtimerIon.kicad_pcb, EggtimerIon.kicad_sch]
2025-11-05 Routing Updates to parts
    [EggtimerIon.kicad_pcb, EggtimerIon.kicad_sch]
2025-11-07 Update Footprints
    [EggtimerIon.kicad_pcb, EggtimerIon.kicad_sch, bom.csv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]
2025-11-07 General Updates
    [F25.kicad_pcb, F25.kicad_sch, bom.csv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]
2025-11-07 Production Files
    [F25.kicad_pcb, bom.csv, designators.csv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]
2025-11-07 MOVE TO SPI
    [F25.kicad_pcb, F25.kicad_sch]
2025-11-07 Finish SPI MS6511
    [F25.kicad_pcb, F25.kicad_sch]
2025-11-07 Add sponsors
    [F25.kicad_pcb]
2025-11-11 Font stuff
    [F25.kicad_pcb]
2025-11-12 Updates to Name
    [bom.csv, designators.csv, positions.csv]
2025-11-12 Update LED Resistors
    [F25.kicad_pcb, F25.kicad_sch]
2025-11-12 LED Updates
    [F25.kicad_pcb, F25.kicad_sch]
2025-11-12 Fix LED Resistors and models
    [F25.kicad_pcb, F25.kicad_sch]
2025-11-12 Update Fabrication
    [BOM-F25.csv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]
2025-11-13 Update Folder Structure
    [BOM-F25.csv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]
2025-11-13 Update images
    [board.step]
2025-11-13 Update Silk to SVG
    [F25.kicad_pcb]
2025-11-13 Add rotate.yml Workflow
    [F25.kicad_pcb]
2025-11-13 MAJOR UPDATES
    [BOM-F25.csv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]
2025-11-13 MAJOR FIXES
    Fixed Power circuitry
    Added usb power support
    Added pulldown to buzzer (thx taz)
    Removed 10k pullup on gpio3
    [BOM-F25.csv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]
2025-11-14 Update 3D View
    [F25.kicad_pcb]
2025-11-14 Rotate board images
2025-11-14 Update 3D Models
    [AP2112K-3.3TRG1--3DModel-STEP-418109.STEP, B2B-PH-K-S--3DModel-STEP-56544.STEP, F25.kicad_pcb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]
2025-12-11 Add FC Code
    [partitions_custom.csv]
2025-12-19 feat: Add yaw
2025-12-19 fix: Add yaw argument to snprintf
    [main.cpp]
2025-12-19 feat: Update landing detection
